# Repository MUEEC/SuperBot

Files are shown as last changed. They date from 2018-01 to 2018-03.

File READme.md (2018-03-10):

# SuperBot 
By MUEEC + MechX 

### Useful links
[esp-idf.readthedocs](https://esp-idf.readthedocs.io/en/v1.0/index.html)

[ESP32 overview](http://espressif.com/en/products/hardware/esp32/overview)

[Superbot gSheet](https://docs.google.com/spreadsheets/d/193m6B4Jjvnffp8MPV1TExg5RMnV4DfvUie1eED_nAe4)

[PCBWay](https://www.pcbway.com/)

[PCBCART](https://www.pcbcart.com/)

### PCB constraints:
[PCBWay capabilities](https://www.pcbway.com/capabilities.html)
[PCBCART std pcb capabilities](https://www.pcbcart.com/pcb-fab/standard-pcb.html)

| Component | Model | Datasheet | Supplier | |
|---|---|---|---|---|
| Microcontroller | esp-32-wroom | https://www.espressif.com/sites/default/files/documentation/esp32_datasheet_en.pdf | https://www.aliexpress.com/item/ESP-32S-ESP-WROOM-32-ESP32-ESP-32-Bluetooth-and-WIFI-Dual-Core-CPU-with-Low/32814324137.html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,searchweb201602_5_10152_10151_10065_10344_10130_10068_10342_10547_10343_10340_10548_10341_10084_10083_10615_10307_10131_10132_10133_10059_10314_10534_100031_10604_10103_10142,searchweb201603_25,ppcSwitch_5&algo_expid=40ad2c8c-2938-46a2-9d3a-9106771881f1-0&algo_pvid=40ad2c8c-2938-46a2-9d3a-9106771881f1&priceBeautifyAB=0 | |
| Battery | Turnigy 2200mAh 1S 20C Lipo | | https://hobbyking.com/en_us/turnigy-2200mah-1s-20c-lipoly-single-cell-1.html | |
| Motor x3 | 170-300 RPM 3-6V Metal Gear | | https://www.aliexpress.com/item/5PCS-Aiyima-Miniature-N20-Gearmotor-DC3-6V-170-350RPM-Steel-Gears-Motor-Robot-Motor-With-Metal/32806511749.html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,searchweb201602_1_10152_10151_10065_10344_10130_10068_10547_10342_10343_10340_10548_10341_10084_10083_10615_10307_10131_10132_10133_10059_10314_10534_100031_10604_10103_10142,searchweb201603_36,ppcSwitch_3&algo_expid=ed9ac777-6257-4ac5-a57d-a63100924402-0&algo_pvid=ed9ac777-6257-4ac5-a57d-a63100924402&priceBeautifyAB=3 | |
| IR Range Finder | Sharp GP2Y0A21YK | https://media.digikey.com/pdf/Data%20Sheets/Sharp%20PDFs/GP2Y0A21YK0F.pdf | https://www.aliexpress.com/item/FREE-SHIPPING-10PCS-LOT-100-NEW-GP2Y0A21YK-SENSOR-DIST-MEASUR-80CM-ANLG-GP2Y0A21YK0F-INCLUDING-WIRES/32249173968.html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,searchweb201602_5_10152_10151_10065_10344_10130_10068_10342_10547_10343_10340_10548_10341_10084_10083_10615_10307_10131_10132_10133_10059_10314_10534_100031_10604_10103_10142,searchweb201603_25,ppcSwitch_5&algo_expid=f3ccdc6a-023b-482e-b9cf-c37fb9346745-0&algo_pvid=f3ccdc6a-023b-482e-b9cf-c37fb9346745&priceBeautifyAB=0 | |
| H bridge | DRV8839DSSR | http://www.ti.com/lit/ds/symlink/drv8839.pdf | https://www.digikey.com.au/product-detail/en/texas-instruments/DRV8839DSSR/296-35701-1-ND/3915296 | |
| Ultrasonic range finder | HC-SR04 | | https://www.aliexpress.com/item/Free-shipping-1pcs-Ultrasonic-Module-HC-SR04-Distance-Measuring-Transducer-Sensor-for-Arduino-Samples-Best-prices/32640823431.html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,searchweb201602_5_10152_10151_10065_10344_10130_10068_10342_10547_10343_10340_10548_10341_10084_10083_10615_10307_10131_10132_10133_10059_10314_10534_100031_10604_10103_10142,searchweb201603_25,ppcSwitch_5&algo_expid=c9000828-80f5-4158-9726-f43c3cd1ecc3-0&algo_pvid=c9000828-80f5-4158-9726-f43c3cd1ecc3&priceBeautifyAB=0 | |
| MPU-9250 | 1428-1019-1-ND | https://store.invensense.com/datasheets/invensense/MPU9250REV1.0.pdf | https://www.digikey.com.au/product-detail/en/tdk-invensense/MPU-9250/1428-1019-1-ND/4626450 | |
| IR reflective sensor | VCNT2020CT-ND | http://www.vishay.com/docs/84285/vcnt2020.pdf https://www.vishay.com/docs/84395/designingvcnt2020.pdf | https://www.digikey.com.au/product-detail/en/vishay-semiconductor-opto-division/VCNT2020/VCNT2020CT-ND/7560298 | |
| SMD LED (0603) | SML-D12U1WT86CT-ND | http://www.rohm.com/web/global/datasheet/SML-D12U1W | https://www.digikey.com.au/products/en?keywords=SML-D12U1WT86CT-ND | |
| SMD RBG LED (0603?) | CLV1L-FKB-CJMNQEGBB7673673CT-ND | http://www.cree.com/led-components/media/documents/CLV1L-FKB-1238.pdf | https://www.digikey.com.au/product-detail/en/cree-inc/CLV1L-FKB-CJMNQEGBB7673673/CLV1L-FKB-CJMNQEGBB7673673CT-ND/7648420 | |
| Shift registers (SI,PO) | | https://assets.nexperia.com/documents/data-sheet/74HC_HCT164.pdf | https://www.digikey.com.au/product-detail/en/nexperia-usa-inc/74HC164D653/1727-2787-1-ND/763377 | |
| USB micro B | | https://cdn.amphenol-icc.com/media/wysiwyg/files/documentation/datasheet/inputoutput/io_usb_micro.pdf https://cdn.amphenol-icc.com/media/wysiwyg/files/drawing/10118194.pdf | https://www.digikey.com.au/product-detail/en/amphenol-fci/10118194-0001LF/609-4618-1-ND/2785382 | |
| Battery management | BQ24079 | http://www.ti.com/lit/ds/symlink/bq24079.pdf | https://www.digikey.com.au/product-detail/en/texas-instruments/BQ24079RGTR/296-24815-1-ND/2094655 | |
| Headers 1x8? 100mil (=0.1in?) pitch | | | | |
| Boost/Buck Converter for motors | TPS61089RNRR | http://www.ti.com/lit/ds/symlink/tps61089.pdf | https://www.digikey.com.au/product-detail/en/texas-instruments/TPS61089RNRR/296-47295-1-ND/7688305 | |
| Buck for controller | AP3435MPTR-G1DICT-ND | https://www.diodes.com/assets/Datasheets/AP3435.pdf | https://www.digikey.com.au/product-detail/en/diodes-incorporated/AP3435MPTR-G1/AP3435MPTR-G1DICT-ND/4505177 | |
| Lin Reg for controller | AP2114H-3.3TRG1DICT-ND | https://www.diodes.com/assets/Datasheets/AP2114.pdf | https://www.digikey.com.au/product-detail/en/diodes-incorporated/AP2114H-3.3TRG1/AP2114H-3.3TRG1DICT-ND/4505142 | |
| USB-UART Bridge | CP2105-F01-GMR | https://www.silabs.com/documents/public/data-sheets/CP2105.pdf https://www.silabs.com/documents/public/errata/cp2105-errata.pdf | https://www.digikey.com.au/product-detail/en/silicon-labs/CP2105-F01-GMR/CP2105-F01-GMRCT-ND/8017817 | |
| Avalanche Diode Array (ESP protection) | SP0503BAHTG | http://www.littelfuse.com/~/media/files/littelfuse/technical%20resources/documents/data%20sheets/sp05xxba.pdf | https://www.digikey.com.au/product-detail/en/littelfuse-inc/SP0503BAHTG/F2715CT-ND/1154322 | |
| Lin Reg for 5v HC-SR04 | MIC5378YC5-TR | http://ww1.microchip.com/downloads/en/DeviceDoc/mic5375.pdf | https://www.digikey.com.au/product-detail/en/microchip-technology/MIC5378YC5-TR/1611-MIC5378YC5-CT-ND/5700662 | |

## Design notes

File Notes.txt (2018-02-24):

http://espressif.com/en/support/download/documents?keys=reference+design
http://espressif.com/en/support/download/overview?keys=&field_type_tid%5B%5D=13
https://www.youtube.com/watch?v=0n6k6GYu_V0
http://espressif.com/sites/default/files/documentation/esp32_hardware_design_guidelines_en.pdf
http://espressif.com/sites/default/files/documentation/esp-wroom-32_datasheet_en.pdf
https://docs.google.com/spreadsheets/d/193m6B4Jjvnffp8MPV1TExg5RMnV4DfvUie1eED_nAe4/edit#gid=0
https://github.com/MUEEC/SuperBot
https://trello.com/b/aEsyQRKa/superbot
dip switch for motors
latching push button for power? (batt-bms or bms-sys)

http://www.ti.com/lit/ds/symlink/lm3478.pdf
http://www.ti.com/lit/ds/symlink/tps63070.pdf
https://www.digikey.com.au/product-detail/en/texas-instruments/TPS63070RNMR/296-44874-1-ND/6217416

https://learn.sparkfun.com/tutorials/logic-levels
https://learn.sparkfun.com/tutorials/voltage-dividers

SCHEMATIC OF ALREADY DESIGNED ESP 32 WROOM DEV BOARD
https://dl.espressif.com/dl/schematics/ESP32-Core-Board-V2_sch.pdf

Parts List:
~~ = done
Controller ~~
Battery ~~
Motor ~~
IR range finder
H bridge ~~
Ultrasonic range finder
LSM9DS1 ~~
MPU-9250
IR reflective sensor
SMD LED (0603) ~~
SMD RBG LED (0603?)
Shift registers (SI,PO) ~
USB micro B ~~
Battery management ~~
Headers 1x8? 100mil (=0.1in?) pitch
Boost/Buck Converter for motors ~~
Buck for controller ~~
LDO for controller ~~

NB:
Run MIC5378YC5 pcb part by Tom
	- Had trouble with the component generator 2d part so I custom did it
Programming via arduino interface?
	- Seems to be possible? Allows use of arduino IDE and language which is good for beginners
how to pull IO0 low for programming with USB-UART conv.
	- IO0 needs to be pulled low for programming mode
	- There seems to be a circuit for this in the example schematic but I'm not sure I understand it
	- Example schematic: https://dl.espressif.com/dl/schematics/ESP32-Core-Board-V2_sch.pdf
		- Look in bottom left corner
LEDS - single resistor possible?
	- Don't think so sadly
JST and wire connectors for battery and range finders
	- Max 5-6 amps from the battery so need wire for that (AWG 21 or lower I think)
Range finder placement and housing
	- Need angle brackets so they can face forward not up.
	- For all 3 sensors I think.

More notes:

4 m3 holes
extra motor output 
swap cp2105 for cp 2102
https://www.digikey.com.au/product-detail/en/silicon-labs/CP2102N-A01-GQFN20/336-3692-ND/6012517

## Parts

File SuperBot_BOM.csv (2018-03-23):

Comment | Description | Designator | Footprint | LibRef | Quantity
DC-DC Buck | AP3435, 1.0MHz, 3.5A, Synchronous Step Down DC-DC Converter | BCK1 | SOP8_AP3435 | DC-DC Buck | 1
 | Imported | BMS1 | RGT16_1P7X1P7 | BQ24079RGTR | 1
TPS61089 | Boost Switching Regulator IC Positive Adjustable 4.5V 1 Output 7A 11-VFQFN | BST1 | VQFN_RNR0011A_1mm | TPS61089 | 1
Battery | Multicell Battery | BT1 | BAT-2 | Battery | 1
4.7uF | Capacitor | C1, C2, C3, C6, C18, C21 | CAP0603R | C | 6
10uF | Capacitor | C4, C23 | CAP0603R | C | 2
22uF | Capacitor | C5, C15, C17 | CAP0805R | C | 3
0.1uF | Capacitor | C7, C8, C9, C10, C11, C12, C13, C14, C22, C24, C25 | CAP0603R | C | 11
2.2uF | Capacitor | C16 | CAP0603R | C | 1
1uF | Capacitor | C19, C20 | CAP0603R | C | 2
10nF | Capacitor | C26 | CAP0603R | C | 1
0.1pF | Capacitor | C27, C28 | CAP0603R | C | 2
RED | LED | CHG, PWR | 0603_LED | LED | 2
RED | LED | D4, D5 | LED0603 | LED | 2
TX LED | LED | D6 | 0603_LED | LED | 1
RX LED | LED | D7 | 0603_LED | LED | 1
SP0503BAHTG | TVS DIODE 5.5VWM 8.5VC SOT143 | DA1 | SOT143_SP0503BAHT | SP0503BAHTG | 1
ESP-32-WROOM | ESP-32-WROOM, WIFI + BT | ESP1 | ESP-32-WROOM | ESP-32-WROOM | 1
H-Bridge | 1.8A , Half Bridge (2), Driver - Fully Integrated, Control and Power Stage | H1, H2, H3 | WSON_0.8mm_DSS0012A | DRV8839DSSR | 3
VCNT2020 | Reflective Optical Sensor with Transistor Output | IR1 | VCNT2020 | VCNT2020 | 1
IR Range Finder | Sharp IR GP2Y0A21YK0F | IRF1 | H3 | IR-Range-Finder | 1
 | Header, 5-Pin, Dual row | JTAG1 | HDR2X5 | Header 5X2 | 1
2.2uH | Inductor | L1, L2 | 744031004 | L | 2
3.3V Reg | AP2114H-3.3TRG1 | LRG1 | SOT223_AP2114 | Reg 3.3V | 1
MIC5375-78 | Linear Voltage Regulator IC Positive Adjustable 1 Output 1.5 V ~ 4.5 V 150mA SC-70-5 | LRG2 | TSOP5_MIC537X | MIC5378YC5 | 1
Motor |  | M1, M2, M3 | MicroMotor_TypeA | Motor | 3
Enable Jumper Motor 1 | Header, 2-Pin | M1J | HDR1X2 | Header 2 | 1
Enable Jumper Motor 2 | Header, 2-Pin | M2J | HDR1X2 | Header 2 | 1
Enable Jumper Motor 3 | Header, 2-Pin | M3J | HDR1X2 | Header 2 | 1
MPU-9250_9DOF | IMU ACCEL/GYRO/MAG I2C/SPI 24QFN | MPU1 | QFN424_MPU-9250 | MPU-9250 | 1
 | Imported | MUX1 | DB24-M | CD74HC4067SM96 | 1
1.13K | Resistor | R1 | RES0603R | R | 1
1.18 | Resistor | R2 | RES0603R | R | 1
1K | Resistor | R3, R4, R50 | RES0603R | R | 3
510K | Resistor | R5 | RES0603R | R | 1
32.5K | Resistor | R6 | RES0603R | R | 1
100K | Resistor | R7, R8, R9, R35, R37, R53, R58, R59 | RES0603R | R | 8
200 | Resistor | R11, R12 | RES0603R | R | 2
180 | Resistor | R13, R14, R15, R16, R17, R18, R19, R20, R21, R22, R23, R24 | RES0603R | R | 12
150K | Resistor | R31 | RES0603R | R | 1
437.19K | Resistor | R32 | RES0603R | R | 1
10K | Resistor | R33, R54, R55, R56, R57 | RES0603R | R | 5
127K | Resistor | R34 | RES0603R | R | 1
17.4K | Resistor | R36 | RES0603R | R | 1
1000K | Resistor | R38 | RES0603R | R | 1
1.7K | Resistor | R39, R43 | RES0603R | R | 2
250K | Resistor | R40 | RES0603R | R | 1
3.3K | Resistor | R41, R46 | RES0603R | R | 2
24K | Resistor | R42 | RES0603R | R | 1
13K | Resistor | R44 | RES0603R | R | 1
220 | Resistor | R45 | RES0603R | R | 1
12K | Resistor | R47, R48 | RES0603R | R | 2
350 | Resistor | R49, R51 | RES0603R | R | 2
5K | Resistor | R52 | RES0603R | R | 1
 | Red, Green, Blue (RGB) 622nm Red, 528nm Green, 468nm Blue LED Indication - Discrete 2V Red, 3.1V Green, 3.1V Blue 4-PLCC | RGB1, RGB2, RGB3, RGB4 | RGB LED | RGB LED | 4
74HC595D | Shift Register | S1, S2 | SOT109-1-M | 74HC595D | 2
DIP SPDT 4P |  | SW2 | DIP SPDT 4P | DIP SPDT 4P | 1
SS8050-G | SS8050-G | T1, T2 | SOT23-SS8050-G | NPN Transistor | 2
Thermistor |  | TS | RES0603R | Thermistor | 1
CP2102N | 336-3694-ND , IC BRIDGE USB TO UART 28QFN | UART1 | QFN28_CP2102n | CP2102N | 1
Ultrasonic Sensor | Header, 4-Pin | US1 | HDR1X4 | Header 4 | 1
USb-Mirco | USb-Mirco, CONN RCPT MCR USB B SMD TH SHLL | USB1 | USB_micro_through | USb-Mirco | 1

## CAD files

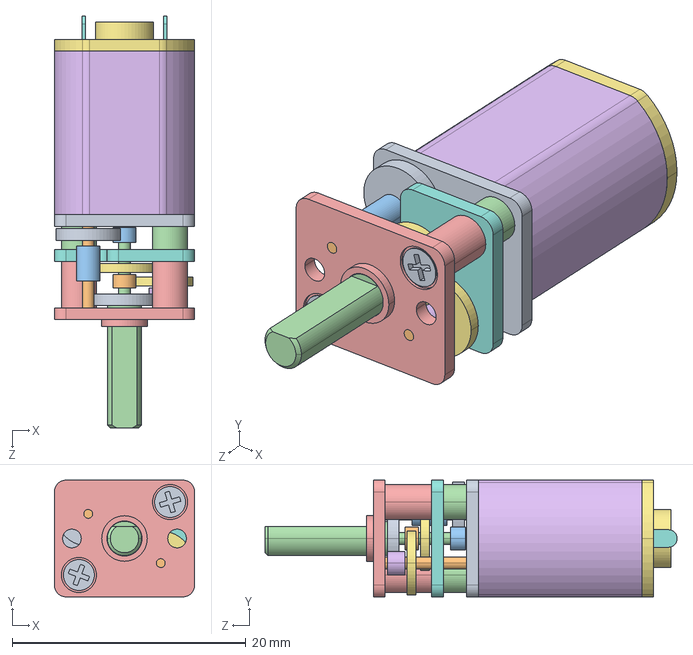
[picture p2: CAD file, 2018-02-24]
Electrical/Pololu - 1_250 Micro gear motor.STEP
12.0 x 10.0 x 35.3 mm

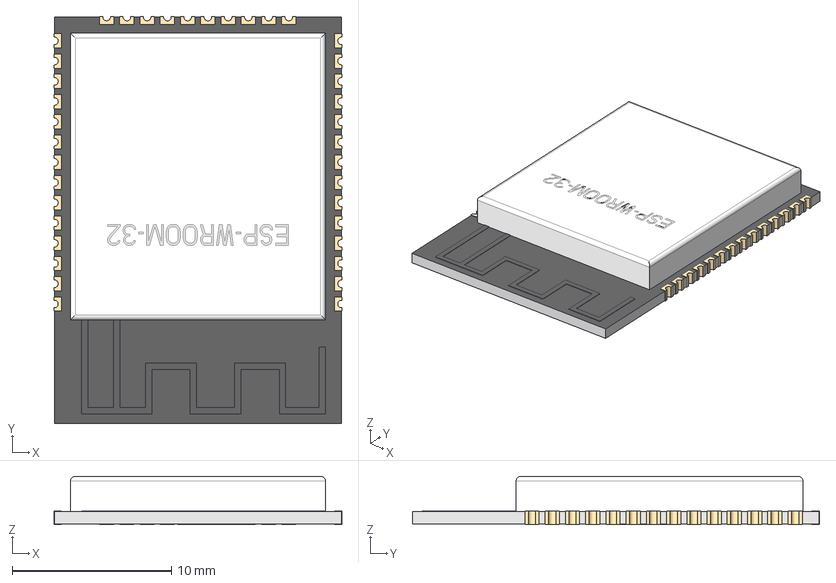
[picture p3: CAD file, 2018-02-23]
Electrical/KiCAD-ESP-WROOM-32.step
18.1 x 25.5 x 3.04 mm

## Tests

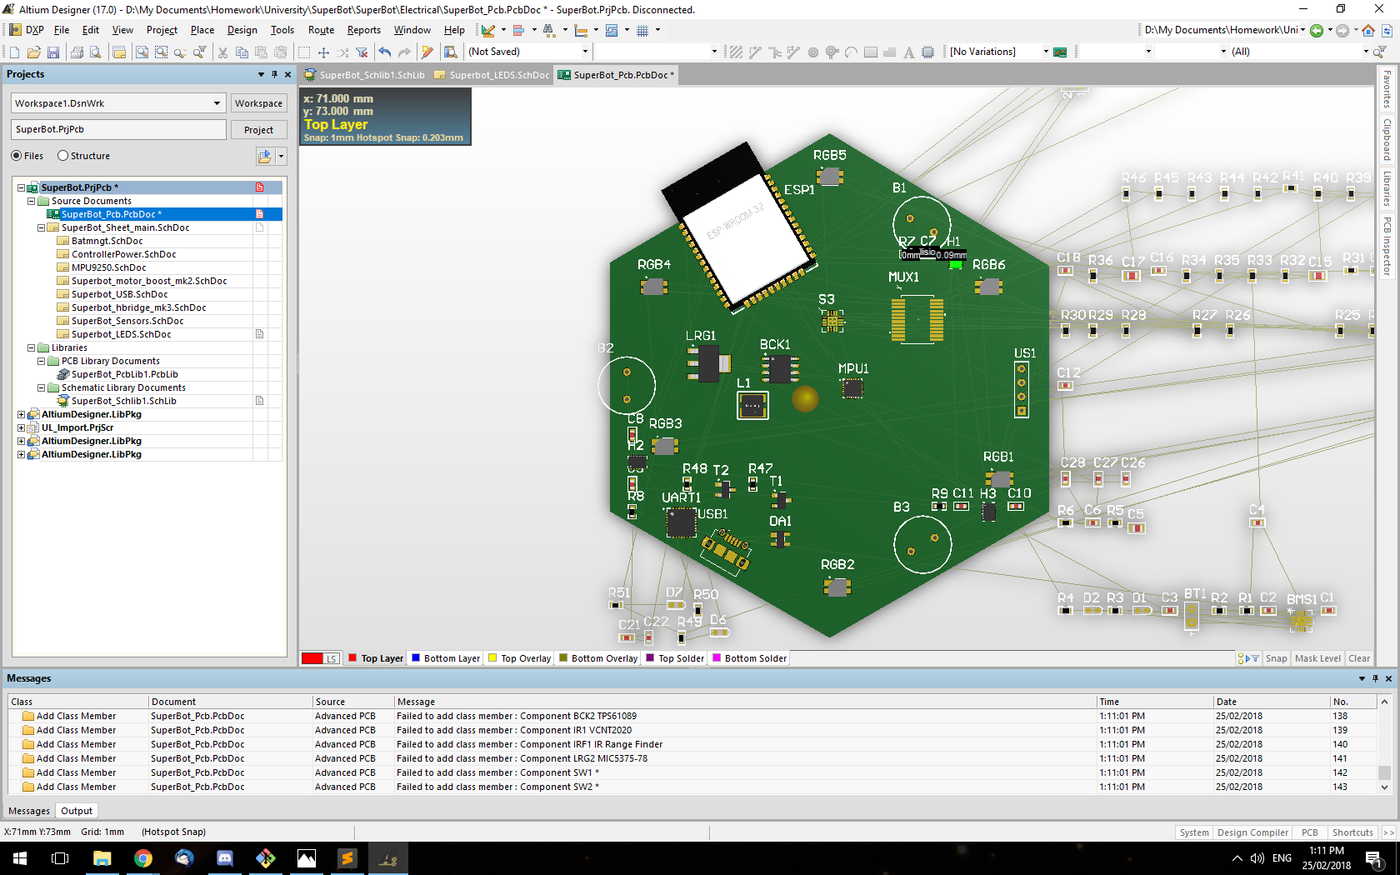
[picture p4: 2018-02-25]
TestPlacement.png

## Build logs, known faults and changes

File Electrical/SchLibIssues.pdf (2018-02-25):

Change Order Report For Project | SuperBot.PrjPcb And SuperBot.PrjPcb
Action Object | Change Document | Status

Add Pins To Nets
Add | BCK1-VCC to V_5.5 | In SuperBot_Pcb.PcbDoc
Add | IRF1-GND to GND | In SuperBot_Pcb.PcbDoc
Add | IRF1-Signal to NetIRF1_Signal | In SuperBot_Pcb.PcbDoc
Add | IRF1-VCC to V_5.5 | In SuperBot_Pcb.PcbDoc
Add | SW1-4 to M3_EN | In SuperBot_Pcb.PcbDoc
Add | SW1-5 to NetR53_1 | In SuperBot_Pcb.PcbDoc
Add | SW1-6 to NetESP1_28 | In SuperBot_Pcb.PcbDoc
Add | SW1-7 to M2_EN | In SuperBot_Pcb.PcbDoc
Add | SW1-8 to NetR53_1 | In SuperBot_Pcb.PcbDoc
Add | SW1-9 to NetESP1_29 | In SuperBot_Pcb.PcbDoc
Add | SW1-10 to M1_EN | In SuperBot_Pcb.PcbDoc
Add | SW1-11 to NetR53_1 | In SuperBot_Pcb.PcbDoc
Add | SW1-12 to NetESP1_30 | In SuperBot_Pcb.PcbDoc
Add | SW2-1 to BMS_EN2 | In SuperBot_Pcb.PcbDoc
Add | SW2-2 to NetR58_1 | In SuperBot_Pcb.PcbDoc
Add | SW2-3 to CH_1.5 | In SuperBot_Pcb.PcbDoc
Add | SW2-4 to BMS_EN1 | In SuperBot_Pcb.PcbDoc
Add | SW2-5 to NetR57_1 | In SuperBot_Pcb.PcbDoc
Add | SW2-6 to CH_0.5 | In SuperBot_Pcb.PcbDoc
Add | SW2-7 to TRST | In SuperBot_Pcb.PcbDoc
Add | SW2-9 to EN | In SuperBot_Pcb.PcbDoc
Add | SW2-10 to EN | In SuperBot_Pcb.PcbDoc
Add | SW2-11 to NetR55_1 | In SuperBot_Pcb.PcbDoc
Add | SW2-12 to NetR54_1 | In SuperBot_Pcb.PcbDoc
Add | T1-BASE to NetR47_2 | In SuperBot_Pcb.PcbDoc
Add | T1-CLCTR to EN | In SuperBot_Pcb.PcbDoc
Add | T1-EMTTR to ESP_CTS | In SuperBot_Pcb.PcbDoc
Add | T2-BASE to NetR48_2 | In SuperBot_Pcb.PcbDoc
Add | T2-CLCTR to IO0 | In SuperBot_Pcb.PcbDoc
Add | T2-EMTTR to NetR47_1 | In SuperBot_Pcb.PcbDoc

Add Component Class Members
Add | SW1 to SuperBot_Sheet_main | In SuperBot_Pcb.PcbDoc
Add | SW2 to SuperBot_Sheet_main | In SuperBot_Pcb.PcbDoc

Add Rooms
Add | Room Batmngt | To SuperBot_Pcb.PcbDoc
(Scope=InComponentClass('Batmngt')) TopLayer
Add | Room ControllerPower | To SuperBot_Pcb.PcbDoc
(Scope=InComponentClass('ControllerPower'))
TopLayer
Add | Room MPU9250 | To SuperBot_Pcb.PcbDoc
(Scope=InComponentClass('MPU9250'))
TopLayer
Add Room Superbot_hbridge_mk3(Scope=InCompone To SuperBot_Pcb.PcbDoc ntClass('Superbot_hbridge_mk3')) TopLayer
Add | Room Superbot_LEDS | To SuperBot_Pcb.PcbDoc
(Scope=InComponentClass('Superbot_LEDS'))
TopLayer
Add Room Superbot_motor_boost_mk2(Scope=InCom To SuperBot_Pcb.PcbDoc ponentClass('Superbot_motor_boost_mk2'))
TopLayer
Add | Room SuperBot_Sensors | To SuperBot_Pcb.PcbDoc
(Scope=InComponentClass('SuperBot_Sensors'))
TopLayer
Add Room SuperBot_Sheet_main(Scope=InComponen To SuperBot_Pcb.PcbDoc tClass('SuperBot_Sheet_main')) TopLayer
Add | Room Superbot_USB | To SuperBot_Pcb.PcbDoc
(Scope=InComponentClass('Superbot_USB'))
TopLayer
Sunday 25-Feb-25/2018 7:40:18 PM | Page 1 of 1

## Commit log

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2018-01-22 Altium file structure started
    [SuperBot.PrjPcb, SuperBot_Pcb.PcbDoc, SuperBot_PcbLib1.PcbLib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]
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2018-01-25 Created project planner .xlsx
    [Batmngt.SchDoc, ProjectPlanning.xlsx]
2018-01-30 multiple schematics added, mk2 versions better
    [ControllerPower.SchDoc, SuperBot.PrjPcb, SuperBot_PcbLib1.PcbLib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]
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2018-02-02 Tidied up a bit
    [ControllerPower.SchDoc, SuperBot_PcbLib1.PcbLib, SuperBot_Schlib1.SchLib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]
2018-02-04 USB-UART and other changes
    [Batmngt.SchDoc, SuperBot.PrjPcb, SuperBot_PcbLib1.PcbLib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]
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2018-02-14 Used the auto annotate feature
    [Batmngt.SchDoc, ControllerPower.SchDoc, SuperBot.PrjPcb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]
2018-02-20 Added MPU9250 schematic WIP
    [MPU9250.SchDoc, SuperBot.PrjPcb]
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2018-02-20 SCH LIB RBG Updated
    [SuperBot_Schlib1.SchLib]
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2018-02-21 Changed passives to use new schlib parts, main sheet,batmngt,controllerPow and motor boost done
    [Batmngt.SchDoc, ControllerPower.SchDoc, SuperBot_Sheet_main.SchDoc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]
2018-02-22 Rotated 90deg and rearranged/tidied
    [Batmngt.SchDoc]
2018-02-22 Converted V_* nets to power rails
    e.g. V_3.3, V_3.4, V_3.4_Buck "Net Labels" are now "VCC Power Ports"
    [ControllerPower.SchDoc, Superbot_hbridge_mk3.SchDoc, Superbot_motor_boost_mk2.SchDoc]
2018-02-22 Converted V_* nets to power rails (cont.)
    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
    [ControllerPower.SchDoc]
2018-02-22 all passives now use schlib parts
    [Batmngt.SchDoc, MPU9250.SchDoc, SuperBot_Sensors.SchDoc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]
2018-02-23 Almost all schematics update with new lib files, USB and BMS not done
    [Batmngt.SchDoc, ControllerPower.SchDoc, MPU9250.SchDoc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]
2018-02-23 UART + MPU Shc Lib Added
    [SuperBot_Schlib1.SchLib]
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2018-02-23 Added net labels for SPI Port to Main Schematic
    [SuperBot_Sheet_main.SchDoc]
2018-02-23 Added SPI Net Labels to MPU schematic
    [MPU9250.SchDoc]
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2018-02-24 Added Sheet symbol to Main for MPU9250
    [SuperBot_Sheet_main.SchDoc]
2018-02-24 Multiple changes apologies for large commit
    [Batmngt.SchDoc, SuperBot_PcbLib1.PcbLib, SuperBot_Schlib1.SchLib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]
2018-02-24 Fixed capacitor value on MIC output
    [SuperBot_Sensors.SchDoc]
2018-02-24 updated main sheet to use new lib comp
    [SuperBot_Sheet_main.SchDoc]
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2018-02-24 Footprint lib tidy up
    [SuperBot_PcbLib1.PcbLib, SuperBot_Schlib1.SchLib]
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2018-02-24 almost missed the MPU
    [MPU9250.SchDoc, SuperBot.PrjPcb]
2018-02-24 MPU Sch: the SPI nets seems weren't on the pins
    When I dragged the component, the other wires stayed connected, but the MOST,SCK, CS nets did not move. I moved them one unit to the right onto the pins. When I drag the component now, these nets mov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
    [MPU9250.SchDoc]
2018-02-24 USB Sch: CH_EN, CH_1.5 nets seemed not on pins
    To confirm, moving CP2102N didn't move the CH_EN and CH_1.5 nets along with them (though you can tell by looking). I added some wire to connect them to their resp. pins.
    [Superbot_USB.SchDoc]
2018-02-24 Set Models to the appropriate footprints (of their components)
    Going Right-Click>Properties and checking the footprint under "Models" in the bottom-right showed they referred to non-existent footprints. I checked the "Link to Library Component" and noted the Mod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
    The offending parts seemed to be:
    DA
    H1
    H2
    H3
    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
    [ControllerPower.SchDoc, Superbot_LEDS.SchDoc, Superbot_USB.SchDoc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]
2018-02-24 Set Models to the appropriate footprints (of their components) (cont.)
    I somehow missed LRG1 and DA, even though those fileswere changed in the last commit
    [ControllerPower.SchDoc, Superbot_USB.SchDoc]
2018-02-24 Fixed Compile errors
    -Redid the Designators with Tools\Annotation\Annotate_Schematics...
    -Moved M1_EN net (on SW1, top-right of Main sheet), 3 units to the left so it's on the appropriate pin (like SW2; due to a mistake in the component sch?)
    -Cut-Re-Pasted USB_DN and USB_DP back onto the wires, since they were apparently off-grid
    [Batmngt.SchDoc, MPU9250.SchDoc, SuperBot.PrjPcb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]
2018-02-25 fixed up broken lib connections & started test route
    [Batmngt.SchDoc, ControllerPower.SchDoc, MPU9250.SchDoc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]
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2018-02-25 Altered Pin Designator of DC-DC Buck Sch
    VCC -> 1
    [SuperBot_Schlib1.SchLib]
2018-02-25 Altered Pin Designators of NPN Transistor Sch
    Swapped their Designators and Display Names for all three pins
    [SuperBot_Schlib1.SchLib]
2018-02-25 Update from Libraries for NPN Transistor and DC-DC Buck
    [ControllerPower.SchDoc, SuperBot.PrjPcb, Superbot_USB.SchDoc]
2018-02-25 Altered pins of IR-Range-Finder Sch
    Swapped Designators and Display Names, changed VCC pin from Input to Power. I note that the datasheet has the pins V_O, GND, VCC, which doesn't match the footprint's square GND through-hole pad being on the end.
    [SuperBot_Schlib1.SchLib]
2018-02-25 Altered pins of IR-Range-Finder Sch (again)
    Rearranged the Designators so the order is GND,VCC,Signal on the footprint (noting that "1" is the square through-hole pad)
    [SuperBot_Schlib1.SchLib]
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2018-02-25 Tried making a DIP SPDT 4P footprint, and attaching it to the DIP SPDT 4P sch
    [SuperBot_PcbLib1.PcbLib, SuperBot_Schlib1.SchLib]
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2018-02-25 problems with updating
    [SuperBot.PrjPcb, SuperBot_Pcb.PcbDoc, SuperBot_Sensors.SchDoc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]
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2018-02-26 Changed PCB Designators to w,h=8mil,36mil (Uni comp is v14.2 btw)
    [SuperBot_Pcb.PcbDoc]
2018-02-26 PCB: Rearranged the LED sch components to give an idea of the pin positions
    [SuperBot_Pcb.PcbDoc]
2018-02-26 PCB: Moved IRF1 resistors R43 R46 next to IRF1
    [SuperBot_Pcb.PcbDoc]
2018-02-26 Sch: Changed the US pins so GND is the square pad
    [SuperBot_Sensors.SchDoc]
2018-02-26 Pcb: Imported from sch to update US pin changes
    [SuperBot_Pcb.PcbDoc]
2018-02-26 Revert "Pcb: Imported from sch to update US pin changes"
    This reverts commit dcee522b30119a74ac346b0feb7adbdb9ca0e85f.
    [SuperBot_Pcb.PcbDoc]
2018-02-26 Revert "Sch: Changed the US pins so GND is the square pad"
    This reverts commit 3d6b795fe7f1053f573271bf927be9a46bb70be8.
    [SuperBot_Sensors.SchDoc]
2018-02-26 Lib: Square Pad for VCC for IR-Range-Finder it is
    So it's VCC GND Signal, corresponding to Square/Isolated Pad, then circle pads.
    The order in the datasheet is Vo, GND, Vcc.
    [SuperBot_Schlib1.SchLib]
2018-02-26 Pcb: Square Pad for VCC for IR-Range-Finder it is
    [SuperBot_Sensors.SchDoc]
2018-02-26 Pcb: Square Pad for VCC for IR-Range-Finder it is (forgot to click save)
    [SuperBot_Pcb.PcbDoc]
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2018-02-28 changed motor boost designator from bck1 to bst1 as it's not a buck conv
    [Superbot_motor_boost_mk2.SchDoc]
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2018-02-28 More sensor routing, swapped OS_ pins on MUX
    [SuperBot_Sensors.SchDoc]
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2018-02-28 Moved IR1 to bottom and routed, swapped OS_ pins again
    [SuperBot_Sensors.SchDoc]
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2018-02-28 Moved & routed sensor stuff, pinswitched leds, edited sch for motors and added a dot for SWs
    [SuperBot.PrjPcb, SuperBot_PcbLib1.PcbLib, SuperBot_Sensors.SchDoc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]
2018-02-28 Fixed pin 10 on SW lib sch
    [SuperBot_Schlib1.SchLib, SuperBot_Sheet_main.SchDoc]
2018-03-01 Hbridges done. Swapped motor pins for neatness
    [Superbot_hbridge_mk3.SchDoc]
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2018-03-01 More routing. Problem with MPU pins being too close together
    [SuperBot.PrjPcb]
2018-03-02 fixed problem with mux_s_ nets, and routed more
    [SuperBot.PrjPcb, SuperBot_Sheet_main.SchDoc]
2018-03-03 Removed SW1, replaced with jumpers. Neater, easier to route.
    [SuperBot_Sheet_main.SchDoc, Superbot_hbridge_mk3.SchDoc]
2018-03-04 Gaze upon my works ye mighty and despair
    [SuperBot.PrjPcb]
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2018-03-09 Updated schematic for removed RGBs, and other in PCB Import list
    [Superbot_LEDS.SchDoc]
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2018-03-10 MPU1 footprint on pcb and lib: shrunk pads 0.25mm->0.2mm, spacing 0.15?->0.2mm
    [SuperBot_PcbLib1.PcbLib]
2018-03-10 Revert "MPU1 footprint on pcb and lib: shrunk pads 0.25mm->0.2mm, spacing 0.15?->0.2mm"
    This reverts commit 7e4c7ea30111e93abff6a9ed71e1f6c251024c49.
    [SuperBot_PcbLib1.PcbLib]
2018-03-10 Violation fix: Adjusted MPU tracks, haven't fully joined track to pads yet
2018-03-10 Shrank PMU pads to 0.24mm, changed DRC to check clearance within footprints, adjusted MPU routing a bit
    [SuperBot_PcbLib1.PcbLib]
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2018-03-23 fixed incorrect resistor comment
    [Batmngt.SchDoc, SuperBot_BOM.csv, SuperBot_BOM.xls]
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2018-07-26 fixing pcb
    [Batmngt.SchDoc, ControllerPower.SchDoc, SuperBot_Sensors.SchDoc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]
